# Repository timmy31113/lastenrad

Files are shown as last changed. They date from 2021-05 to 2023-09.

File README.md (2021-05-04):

# lastenrad
Control system for a prototype cargo bike with a bio-electric hybrid drivetrain concept

This project contains the code for an Arduino controlling the electric systems of a three wheeled Dutch-style cargo bike. 

- A synchronous permanently commutated three-phase AC hub motor drives the rear wheel. 
It is powered by an external motor controller with current and movement direction control.
The motor and controller also allow a regenerative braking function.

- The cyclists pedals into a synchronous permanently commutated three-phase AC generator with a gear transmission.
The generator load is regulated by a power-MOSFET performing PWM after rectification. 
A current sensor indicates how much power the cyclist is putting into the generator.

- The UI provides adjustment options for the desired degree of electric assist and the target pedaling RPM and torque.

The system aims to simulate an automatic CVT gearbox and the goal is an intuitive and comfortable driving experience 
that allows the cyclist to concentrate on the road situation while maintaining optimal power delivery to the wheel.

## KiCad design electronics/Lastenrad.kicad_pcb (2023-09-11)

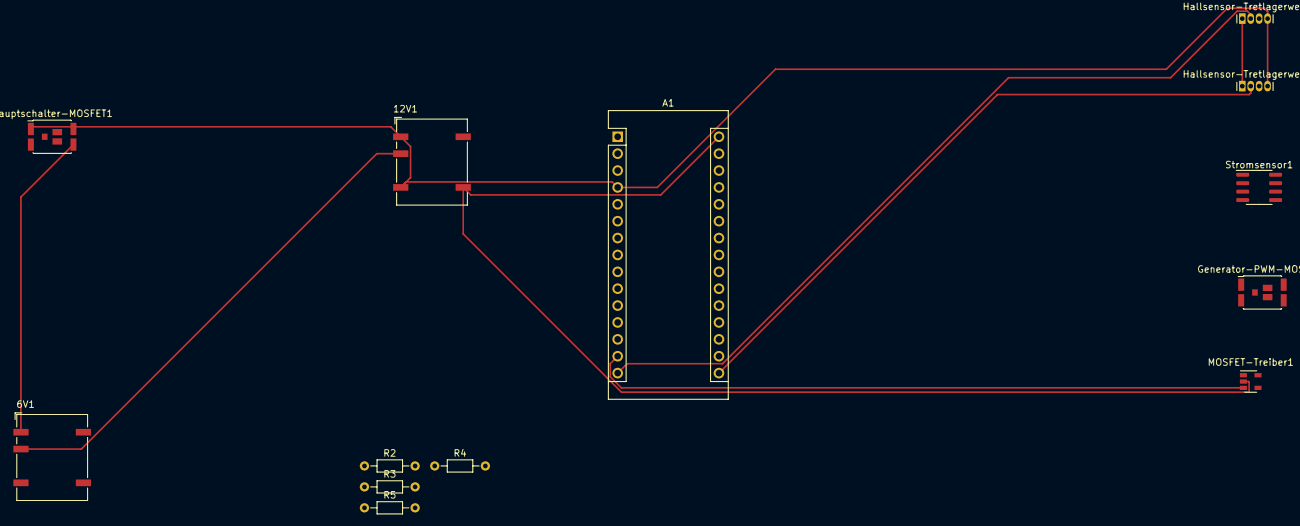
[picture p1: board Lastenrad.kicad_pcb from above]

Board: 2 copper layers, 13 parts (0 on the bottom side), 14 nets.

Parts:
6V1, 12V1: NXE2S1215MC; Converter_DCDC_muRata_NXExSxxxxMC_SMD
A1: Arduino_Nano_v3.x; Arduino_Nano
Generator-PWM-MOSFET1: BSB044N08NN3; DirectFET_MN
Hallsensor-Tretlagerwelle-1, Hallsensor-Tretlagerwelle-2: A1363xKTTN-1; Allegro_SIP-4
Hauptschalter-MOSFET1: BSB044N08NN3; DirectFET_MN
MOSFET-Treiber1: MCP1416; SOT-23-5
R2, R4: 100k; R_Axial_DIN0204_L3.6mm_D1.6mm_P7.62mm_Horizontal
R3, R5: 47k; R_Axial_DIN0204_L3.6mm_D1.6mm_P7.62mm_Horizontal
Stromsensor1: ACS712xLCTR-05B; SOIC-8_3.9x4.9mm_P1.27mm

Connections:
GND: 6V1.1, 6V1.7, 12V1.1, 12V1.7, A1.29, Generator-PWM-MOSFET1.3, Hallsensor-Tretlagerwelle-1.4, Hallsensor-Tretlagerwelle-2.4, Hauptschalter-MOSFET1.1, MOSFET-Treiber1.4, R3.2, R5.2, Stromsensor1.5
unnamed: 6V1.3, 12V1.3
unnamed: 12V1.8, A1.30, MOSFET-Treiber1.2
unnamed: A1.5, R4.2, R5.1
unnamed: A1.10, R2.2, R3.1
unnamed: A1.14, MOSFET-Treiber1.3
unnamed: A1.15, Hallsensor-Tretlagerwelle-2.2
unnamed: A1.16, Hallsensor-Tretlagerwelle-1.2
unnamed: A1.19, Stromsensor1.7
unnamed: A1.27, Hallsensor-Tretlagerwelle-1.1, Hallsensor-Tretlagerwelle-2.1, Stromsensor1.8
unnamed: Stromsensor1.1, Stromsensor1.2
unnamed: Generator-PWM-MOSFET1.1, Stromsensor1.3, Stromsensor1.4
unnamed: Generator-PWM-MOSFET1.2, MOSFET-Treiber1.5
unnamed: R2.1, R4.1

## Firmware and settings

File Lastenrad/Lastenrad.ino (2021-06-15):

//Rechtliche Maximalwerte fuer ein Pedelec gemaess StVZO:
#define MAX_PEDELEC_LEISTUNG_WATT 250 //Watt
#define MAX_PEDELEC_GESCHWINDIGKEIT_KMH 25 //km/h
#define MAX_SCHIEBEHILFE_GESCHWINDIGKEIT_KMH 6 //km/h

#define PIN_LEISTUNG 10
#define PIN_GENERATORWIDERSTAND 11
#define PIN_RUECKWAERTS 4
#define PIN_HALL_A 7
#define PIN_HALL_B 2
#define PIN_GEN_HALL_A 3
#define PIN_GEN_HALL_B 12
#define PIN_REKUPERATION 9

#define APIN_GENERATORLEISTUNG 0
#define APIN_UNTERSTUETZUNG 1
#define APIN_TRETWIDERSTAND 2
#define APIN_BREMSHEBEL 3

//Pins fuer spaetere Erweiterungen, die bereits am Stecker verbunden sind
//#define PIN_AUX_1 13
//#define PIN_AUX_2 5

#define GESCHWINDIGKEIT_ERMITTELN_INTERVAL 5 //mal pro Sekunde
#define MOTORSTEUERUNG_INTERVAL 20 //mal pro Sekunde
#define MILLISEKUNDEN_PRO_SEKUNDE 1000
#define GESCHWINDIGKEIT_UMRECHNUNGSFAKTOR 278 //mm/s entsprechen 1 km/h
#define MAX_PEDELEC_GESCHWINDIGKEIT MAX_PEDELEC_GESCHWINDIGKEIT_KMH * GESCHWINDIGKEIT_UMRECHNUNGSFAKTOR
#define MAX_SCHIEBEHILFE_GESCHWINDIGKEIT MAX_SCHIEBEHILFE_GESCHWINDIGKEIT_KMH * GESCHWINDIGKEIT_UMRECHNUNGSFAKTOR

#define UNTERSTUETZUNG_KENNLINIE_TEILER 7000 //generatorleistung^2 / TEILER + OFFSET
#define UNTERSTUETZUNG_KENNLINIE_OFFSET -2 //generatorleistung^2 / TEILER + OFFSET

#define MOTORPOLE 46
#define RADUMFANG 1756 //mm
#define NENNSPANNUNG 36 //Volt
#define NENNSTROM 30 //Ampere - Entspricht 100% am Pin Leistung
#define VOLLE_LEISTUNG 255 // 100% Leistungssignal
#define MAX_GESCHWINDIGKEIT_MAX_UNTERSTUETZUNG_LEISTUNG (VOLLE_LEISTUNG * MAX_PEDELEC_LEISTUNG_WATT) / (NENNSTROM * NENNSPANNUNG) // Leistungssignal bei 25 km/h und Volllast

//Elektrische Leistungsbegrezung:
//Durch die elektrische Leistungsbegrenzung wird gewaehrleistet, dass die erlaubte Unterstuetzungsleistung niemals ueberschritten wird. Da der Wirkungsgrad <= 100% ist, ist das physikalisch nicht moeglich.
//Leistung = Drehmoment * Drehzahl
//Leistung = Spannung * Strom
//Spannung und Strom sind bekannt. Drehzahl ist bekannt. Das Drehmoment ist linear zum Strom.
//Das Drehmoment ist nicht bekannt, aber der genaue Wert ist fuer die Leistungsbegrenzung auch nicht so wichtig, weil sicher ist dass die abgegebene mechanische Leistung niemals die elektrische Leistung uebersteigt.
//Bei 36 V liegt der Strom bei 250 W / 36 V = ~7 A.
//Bei der Fahrgeschwindigkeit von 25 km/h und voller elektrischer Leistung 250 W nehme ich die Drehzahl 1 (einheitenlos) und das Drehmoment 1 (einheitenlos) an.
//Diese beiden Variablen muessen sich so verhalten, dass ihr Produkt niemals groesser als 1 wird, dann ist sichergestellt, dass die mechanische Leistung auch 250 Watt nicht uebersteigt.
//Das bedeutet, bei einer Drehzahl von 0.5 (Geschwindigkeit 12.5 km/h) kann das Drehmoment 2 betragen, bei Drehzahl 0.25 kann das Drehmoment 4 sein und so weiter.
//Rechnung: leistung = (MAX_GESCHWINDIGKEIT_MAX_UNTERSTUETZUNG_LEISTUNG * MAX_PEDELEC_GESCHWINDIGKEIT) / geschwindigkeit

#define GENERATORSTROM_MAX 25 //Ampere - Wenn das Strommess-IC ein 100% Signal gibt
#define GENERATORSTROM_MAX_SIGNAL 1023 // 100% Eingangssignal - Bedeutet maximaler positiver Stromfluss am Strommess-IC
#define GENERATOR_UMRECHNUNGSFAKTOR GENERATORSTROM_MAX * VOLLE_LEISTUNG
#define GENERATOR_UMRECHNUNGSTEILER (GENERATORSTROM_MAX_SIGNAL / 2) * NENNSTROM
//Rechnung: Ausgabeleistung = (Eingabeleistung * GENERATOR_UMRECHNUNGSFAKTOR) / GENERATOR_UMRECHNUNGSTEILER

uint16_t geschwindigkeit = 0; // in Millimeter pro Sekunde! 1000 mm/s = 1 m/s (278 mm/s = 1 km/h)
volatile bool rueckwaertsIst = false;
bool rueckwaertsSoll = false;
uint16_t unterstuetzung = 0;
uint16_t tretwiderstand = 0;
uint16_t bremshebel = 0;
uint8_t leistung = 0;
uint16_t generatorleistung = 0;
uint8_t ausgabeleistungNachGenerator = 0;
uint8_t rekuperation = 0;

volatile uint8_t motorInkrementZaehler = 0;
uint8_t motorInkrementLetzterZaehlerstand = 0;
uint32_t zeit = 0;

void setup() {
  // put your setup code here, to run once:
  pinMode(PIN_LEISTUNG, OUTPUT);
  pinMode(PIN_GENERATORWIDERSTAND, OUTPUT);
  pinMode(PIN_RUECKWAERTS, OUTPUT);
  pinMode(PIN_REKUPERATION, OUTPUT);

  pinMode(PIN_HALL_A, INPUT);
  pinMode(PIN_HALL_B, INPUT);

  pinMode(PIN_GEN_HALL_A, INPUT);
  pinMode(PIN_GEN_HALL_B, INPUT);

  attachInterrupt(digitalPinToInterrupt(PIN_HALL_A), motorHallISR, CHANGE);
  attachInterrupt(digitalPinToInterrupt(PIN_GEN_HALL_A), generatorISR, CHANGE);

}

void loop() {
  // put your main code here, to run repeatedly:
  if (millis() != zeit) {
    zeit = millis();
    zeitfunktionen();
  }
  
}

void zeitfunktionen() {
  if (zeit % (MILLISEKUNDEN_PRO_SEKUNDE / GESCHWINDIGKEIT_ERMITTELN_INTERVAL) == 0) {
    noInterrupts();
    int8_t schritte = motorInkrementZaehler - motorInkrementLetzterZaehlerstand;
    motorInkrementLetzterZaehlerstand = motorInkrementZaehler;
    interrupts();
    geschwindigkeit = (schritte * RADUMFANG) / MOTORPOLE;

    unterstuetzung = analogRead(APIN_UNTERSTUETZUNG);
    tretwiderstand = analogRead(APIN_TRETWIDERSTAND);
    analogWrite(PIN_GENERATORWIDERSTAND, zehnBitInAchtBitUmwandeln(tretwiderstand));
  }
  if (zeit % (MILLISEKUNDEN_PRO_SEKUNDE / MOTORSTEUERUNG_INTERVAL) == 0) {
    generatorleistungMessen();
    if (rueckwaertsIst == rueckwaertsSoll) {
      if (geschwindigkeit > MAX_PEDELEC_GESCHWINDIGKEIT) {
        leistung = ausgabeleistungNachGenerator;
      }
      else {
        leistung = ausgabeleistungNachGenerator + unterstuetzungsleistungBerechnen();
      }
    }
    else {
      rekuperation = ausgabeleistungNachGenerator; // TODO: Passende Rekuperationsstärke anhand der Generatorleistung berechnen
    }

    bremshebel = analogRead(APIN_BREMSHEBEL);
    uint8_t manuelleRekuperation = zehnBitInAchtBitUmwandeln(bremshebel);
    if (manuelleRekuperation > rekuperation) {
      rekuperation = manuelleRekuperation;
    }

    analogWrite(PIN_LEISTUNG, leistung);
  }
}

void motorHallISR() {
  bool vorwaerts = digitalRead(PIN_HALL_A) == digitalRead(PIN_HALL_B);
  if (vorwaerts) {
    motorInkrementZaehler++;
  }
  else {
    motorInkrementZaehler--;
  }
  rueckwaertsIst = !vorwaerts;
}

void generatorISR() {
  //TODO: Richtung erkennen, optional Drehzahl ermitteln
}

uint8_t zehnBitInAchtBitUmwandeln(uint16_t zehnBitWert) {
  return (uint8_t)(zehnBitWert >> 2);
}

void analogeingabenAbfragen() {
  generatorleistung = analogRead(APIN_GENERATORLEISTUNG);
  unterstuetzung = analogRead(APIN_UNTERSTUETZUNG);
  tretwiderstand = analogRead(APIN_TRETWIDERSTAND);
  bremshebel = analogRead(APIN_BREMSHEBEL);
}

void generatorleistungMessen() {
  generatorleistung = analogRead(APIN_GENERATORLEISTUNG);
  if (generatorleistung < 512) {
    ausgabeleistungNachGenerator = 0;
  }
  else {
    ausgabeleistungNachGenerator = ((generatorleistung - 512) * GENERATOR_UMRECHNUNGSFAKTOR) / GENERATOR_UMRECHNUNGSTEILER;
  }
}

uint8_t unterstuetzungsleistungBerechnen() {
  return constrain(
    ((generatorleistung * generatorleistung) / UNTERSTUETZUNG_KENNLINIE_TEILER + UNTERSTUETZUNG_KENNLINIE_OFFSET), 
    0, (MAX_GESCHWINDIGKEIT_MAX_UNTERSTUETZUNG_LEISTUNG * MAX_PEDELEC_GESCHWINDIGKEIT) / geschwindigkeit);
}

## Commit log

2021-05-06 Changed generator pinout
    The generator now uses only two sensors. The two now-free additional pins are reserved for future add-ons and are physically linked up to the dashboard connector. This commit reflects that design cha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
2021-06-15 Changed the power control
    Output power of the motor is now calculated depending on speed, torque,
    current and voltage. This ensures that the motor never puts out more
    power than legally allowed, while at the same time still allowing a
    reasonably high current in low efficiency situations (accelerating from a
    standstill or on steep grades).
2023-09-11 Added circuit diagrams to version control
    [Lastenrad grobe Verkabelung.kicad_pcb, Lastenrad grobe Verkabelung.sch, Lastenrad-alt-Schrittmotor.sch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]
2025-05-29 Updated circuit diagrams file format version
    From version 3 to version 5
    [Lastenrad.kicad_sch]
2025-05-29 Circuit diagram: Moved motor and motor controller
    Slight adjustments to the positioning to make the connection between
    different physical section more clear
    [Lastenrad.kicad_sch]
2025-07-06 Circuit diagram: Resistor values
    My dad added sensible resistor values all around the circuit diagram
    [Lastenrad.kicad_sch]
2025-07-06 gitignore: New KiCad backup files are now ignored
